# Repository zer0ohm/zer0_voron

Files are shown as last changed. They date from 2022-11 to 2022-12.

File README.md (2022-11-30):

# zer0_voron
## About zer0_voron
A repository for compiling modified parts, or a [hashtag](https://twitter.com/search?q=%23zer0_voron) to be added to tweets about VORON.

## BOM
Under development: It is a modification of an existing component, but it has never been tested and is "very" experimental. (To be tested soon, but undecided.)
### Shoiko(背負子)
 * Rear mounting of electrical components mod for VORON2.4
 * din_rail_mount_a/b inspired from [SnakeOil-XY](https://github.com/SnakeOilXY/SnakeOil-XY/blob/master/BETA2_Release/STLs/Panels/Back-panel/Bottom/4x_din-holder.stl)
 
| Part | Qty | Sourcing | Description/Note |
|---|---|---| --- |
| din_rail_mount_x2 | 2 | Print part([STEP](./CAD/din_rail_mount_x2.step) or [STL](./STLs/din_rail_mount_x2.stl)) |  |
| SHCS M3x** | 2 | Local store | Length are TBD. |
| M3 Roll-in T-Nut | 2 | [AliExpress](https://www.aliexpress.com/item/32805163712.html) |  |
| SB2040 Cable-harness <br> or <br> 2-wire 18AWG Robot Cable(3 meter) + 2-wire AWG22 Robot Cable(3 meter) | 1 | [AliExpress](https://www.aliexpress.com/item/1005004819126687.html) <br> or <br> [Misumi(AWG18)](https://jp.misumi-ec.com/vona2/detail/222000262826/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) + <br> [Misumi(AWG22)](https://jp.misumi-ec.com/vona2/detail/222000262826/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)| Length are TBD. See [Cable Processing](./Docs/cable_processing.md) |
| RJ11 Cable | 1 | [Misumi](https://jp.misumi-ec.com/vona2/detail/110500076440/?HissuCode=CBLRJ050-666-S-07-SV) | For BTT Octopus only. See [Cable Processing](./Docs/cable_processing.md) |
| Toolhead PCB | 1 | [AliExpress](https://www.aliexpress.com/item/1005004675264551.html) | AliExpress's link is example for in Stealthburner. |
| BHCS M5x10 | 2 | Stock or Local store | Replace of screws due to removal of "XY Cable Chain Bridge". |

### Modified Corner Brackets
 * Attempt to determine if printed brackets can be used to strengthen rigidity
 * model based Misumi's HBLFSN5(2mm narrower to avoid interference with Z_Idler)

| Part | Qty | Sourcing | Description/Note |
|---|---|---| --- |
| 2020Frame Corner Bracket 18mmWide | 12 | Print part([STEP](./CAD/2020_CornerBracket_18mm_x12.step) or [STL](./STLs/2020_CornerBracket_18mm_x12.stl)) ||
| SHCS M5x10 | 24 | Local store |  |
| M5 Roll-in T-Nut | 24 | [AliExpress](https://www.aliexpress.com/item/32805163712.html) |  |
| z_belt_cover_a_x2 | 2 | Print part([STEP](./CAD/z_belt_cover_a_x2_mod.step) or [STL](./STLs/z_belt_cover_a_x2_mod.stl)) | Use existing screws and nuts for mounting. |
| z_belt_cover_b_x2 | 2 | Print part([STEP](./CAD/z_belt_cover_b_x2_mod.step) or [STL](./STLs/z_belt_cover_b_x2_mod.stl)) | Use existing screws and nuts for mounting. |

### XYEndstop PCB for X_Carriage
 * Endstop PCB utilizing the switch mounting holes on the back side of X_Carriage 

| Part | Qty | Sourcing | Description/Note |
|---|---|---| --- |
| Endstop PCB | 1 | order PCB yourself([KiCad](./KiCad/V2-X_carriage_XYEndSW)) or [Single item PCB from me](https://zer0ohm.booth.pm/) ||
| Self-tapping screw M2x12 or M2x14 | 2 | Local store or [AliExpress](https://www.aliexpress.com/item/1005002306042593.html) | PCB mount screw |
| D2F-L3-A1 microswitch | 1 | Digikey or Mouser or Local store | X Endstop |
| D2F-L3 microswitch | 1 | Digikey or Mouser or Local store | Y Endstop |
| JST-XH S3B-XH-A | 1 | Digikey or Mouser or Local store |  |
| JST XH XHP-3 | 1 | Digikey or Mouser or Local store | Qty is the number used on this PCB only, the number may vary depending on the connection point. |

### Front Skirt PowerUI Mod(for 350mm build only)
 * Mod to bring "inlet and switch"(PowerUI) to front skirt
 * Can divert parts used in existing front_skirt_a and power_inlet_filtered

| Part | Qty | Sourcing | Description/Note |
|---|---|---| --- |
| front_skirt_a_mod | 1 | Print part([STEP](./CAD/front_skirt_a_mod.step) or [STL](./STLs/front_skirt_a_mod.stl)) ||
| [Optional] power_inlet_filtered_mod | 1 | Print part([STEP](./CAD/power_inlet_filtered_mod.step) or [STL](./STLs/power_inlet_filtered_mod.stl)) | Optional part. May use original parts. |

## Klipper_Configs
* Config for BTT Octopus+Mellow SB2040
* based [VORON's config](https://github.com/VoronDesign/Voron-2/blob/Voron2.4/firmware/klipper_configurations/Octopus/Voron2_Octopus_Config.cfg) and [Mellow/KlipperCN's config](https://mellow.klipper.cn/#/board/fly_sb2040/cfg)

| File | Description/Note |
|---|---|
| printer.cfg | |
| steppers.cfg | XYZ motor drive settings |
| toolhead.cfg | SB2040 settings |
| octopus_heatmanage.cfg | Bed-heater and FAN(excl toolhead fans) control |
| neopixel.cfg | lighting settings in chamber |
| macros.cfg | |
| display.cfg | BTT Mini12864 settings |

## What is Shoiko?
Shoiko(背負子)  is an Japanese word meaning "backpack". (naming inspired from [Kirigami](https://github.com/christophmuellerorg/voron_0_kirigami_bed).)

## License
This design are partially derived from the existing Voron parts and hence follow the same License, [GNU GPLv3](https://www.gnu.org/licenses/gpl-3.0.html).

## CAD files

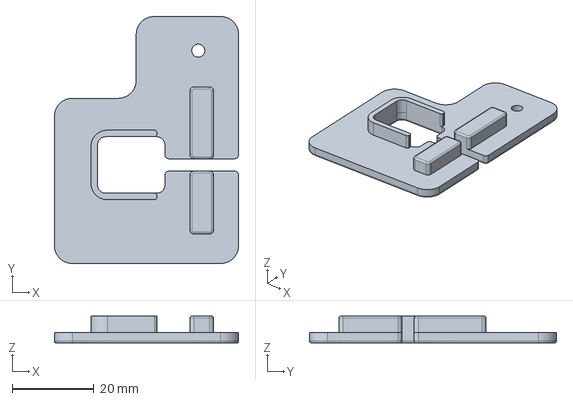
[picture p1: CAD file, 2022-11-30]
CAD/z_belt_cover_a_x2_mod.step
45.0 x 60.4 x 6.60 mm

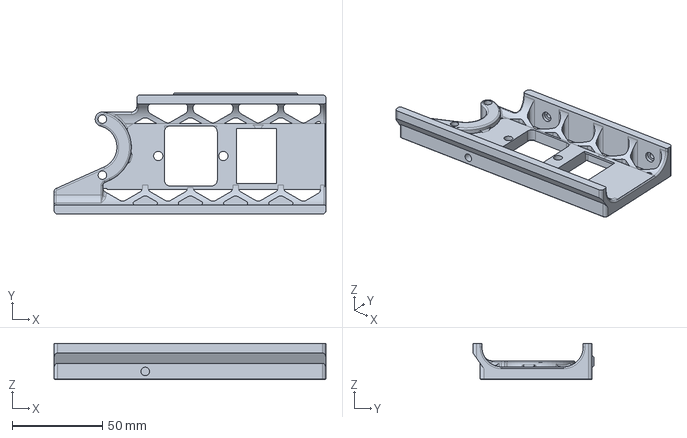
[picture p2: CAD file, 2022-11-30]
CAD/front_skirt_a_mod.step
150.5 x 67.0 x 20.0 mm

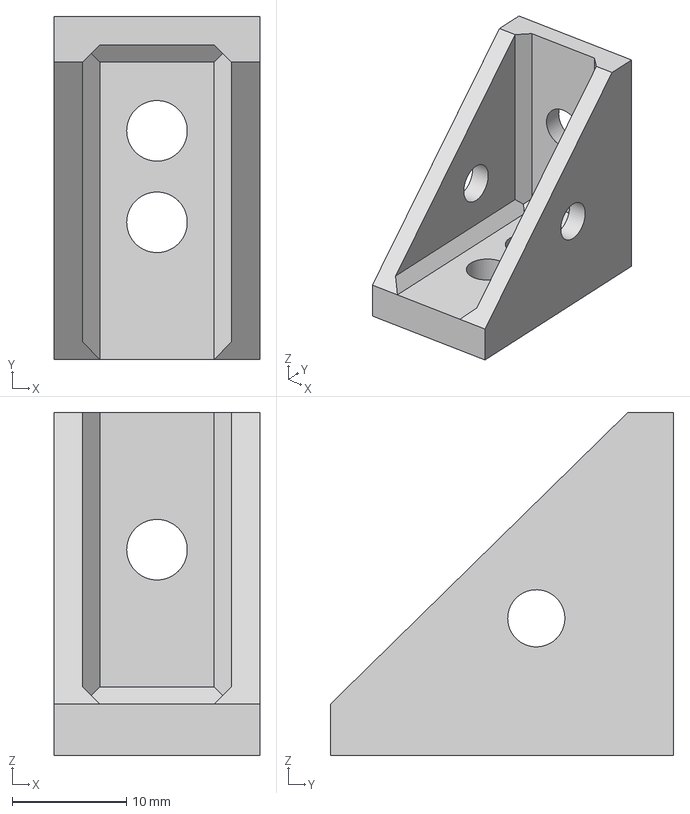
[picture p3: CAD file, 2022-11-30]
CAD/2020_CornerBracket_18mm_x12.step
18.0 x 30.0 x 30.0 mm

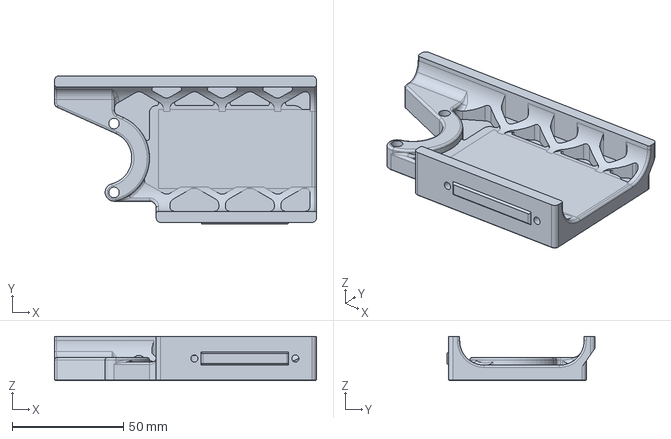
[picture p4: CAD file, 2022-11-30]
CAD/power_inlet_filtered_mod.step
118.0 x 66.8 x 20.0 mm

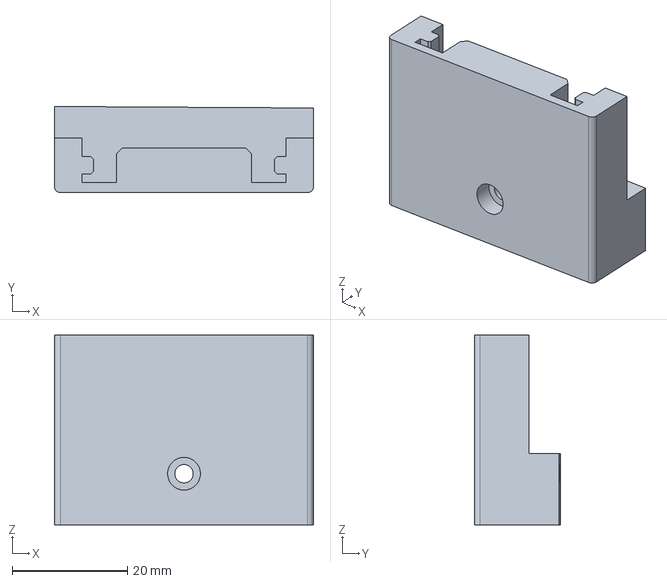
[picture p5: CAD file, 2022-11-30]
CAD/din_rail_mount_x2.step
45.0 x 15.0 x 33.0 mm

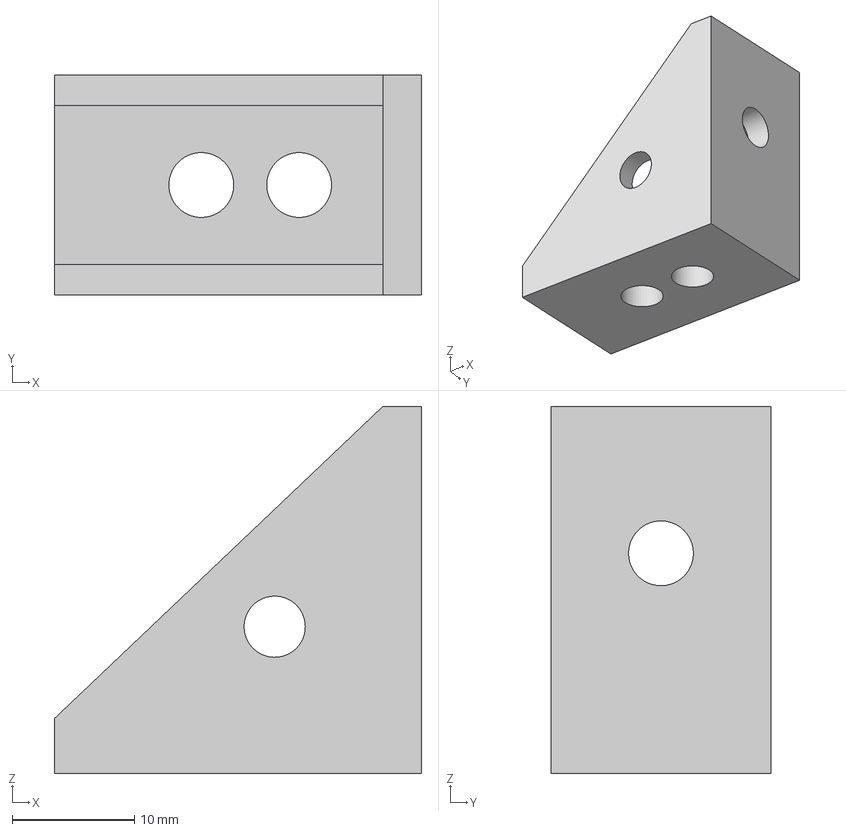
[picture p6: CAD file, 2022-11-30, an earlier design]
CAD/__archive/2020_CornerCube-18mm.step
30.0 x 18.0 x 30.0 mm

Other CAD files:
CAD/z_belt_cover_b_x2_mod.step
CAD/__archive/2020_CornerCube-18mm.f3d
STLs/2020_CornerBracket_18mm_x12.stl
STLs/din_rail_mount_x2.stl
STLs/front_skirt_a_mod.stl
STLs/z_belt_cover_b_x2_mod.stl

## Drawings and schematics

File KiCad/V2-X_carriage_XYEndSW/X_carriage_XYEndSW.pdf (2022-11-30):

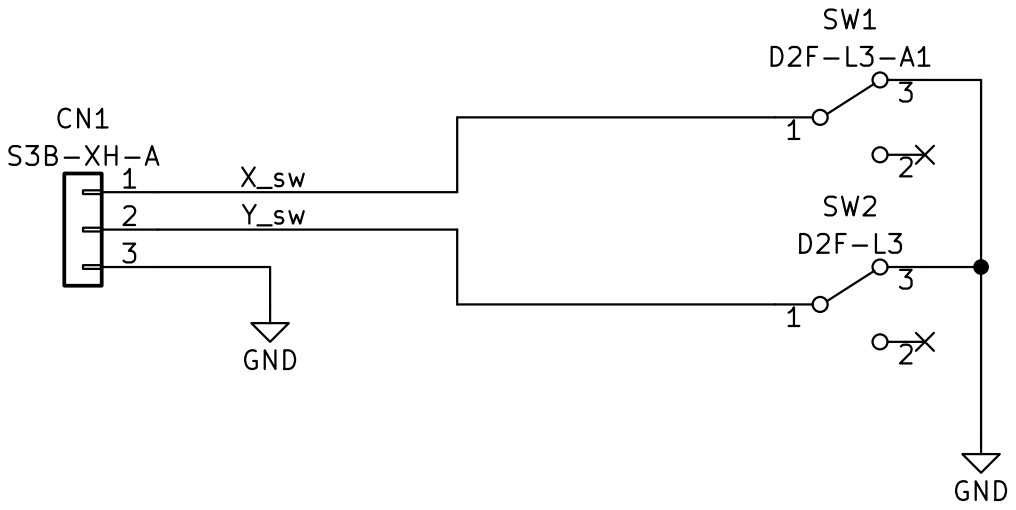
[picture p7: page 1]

File: X_carriage_XYEndSW.kicad_sch Sheet: / GND GND

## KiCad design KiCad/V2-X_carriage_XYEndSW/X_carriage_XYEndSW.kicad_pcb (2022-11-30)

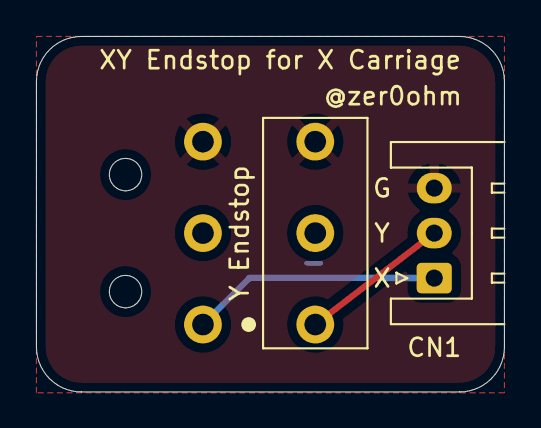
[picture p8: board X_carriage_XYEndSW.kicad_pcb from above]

Board: 2 copper layers, 26.0 x 19.8 mm, 3 parts (1 on the bottom side), 3 nets.

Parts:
CN1: S3B-XH-A; JST_XH_S3B-XH-A_1x03_P2.50mm_Horizontal
SW1: D2F-L3-A1; D2F-x_A1
SW2: D2F-L3; D2F-x_T

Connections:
/X_sw: CN1.1, SW1.1 (A)
/Y_sw: CN1.2, SW2.1 (B)
GND: CN1.3, SW1.3 (B), SW2.3 (A)

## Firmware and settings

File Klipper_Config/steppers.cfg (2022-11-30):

#####################################################################
#   X/Y Stepper Settings (G-Zeroのモータ制御設定を持ってくる予定)
#####################################################################

##  B Stepper - Left
##  Connected to MOTOR_0
##  Endstop connected to DIAG_0
[stepper_x]
step_pin: PF13
dir_pin: !PF12
enable_pin: !PF14
rotation_distance: 40
microsteps: 32
full_steps_per_rotation:200  #set to 400 for 0.9 degree stepper
endstop_pin: PG6
position_min: 0
##--------------------------------------------------------------------

##  Uncomment for 350mm build
position_endstop: 350
position_max: 350

homing_speed: 25   #Max 100
homing_retract_dist: 5
homing_positive_dir: true

##  Make sure to update below for your relevant driver (2208 or 2209)
[tmc2209 stepper_x]
uart_pin: PC4
interpolate: true # default: false
run_current: 0.8 # 1.2(If you use LDO-42STH48-2504AC)
sense_resistor: 0.110
stealthchop_threshold: 0

##  A Stepper - Right
##  Connected to MOTOR_1
##  Endstop connected to DIAG_1
[stepper_y]
step_pin: PG0
dir_pin: !PG1
enable_pin: !PF15
rotation_distance: 40
microsteps: 32
full_steps_per_rotation:200  #set to 400 for 0.9 degree stepper
endstop_pin: PG9
position_min: 0
##--------------------------------------------------------------------

##  Uncomment for 350mm build
position_endstop: 350
position_max: 350

homing_speed: 25  #Max 100
homing_retract_dist: 5
homing_positive_dir: true

##  Make sure to update below for your relevant driver (2208 or 2209)
[tmc2209 stepper_y]
uart_pin: PD11
interpolate: true # default: false
run_current: 0.8
sense_resistor: 0.110
stealthchop_threshold: 0
 
#####################################################################
#   Z Stepper Settings
#####################################################################

## Z0 Stepper - Front Left
##  Connected to MOTOR_2
##  Endstop connected to DIAG_2
[stepper_z]
step_pin: PF11
dir_pin: !PG3
enable_pin: !PG5
rotation_distance: 40
gear_ratio: 80:16
microsteps: 32
endstop_pin: PG10
##  Z-position of nozzle (in mm) to z-endstop trigger point relative to print surface (Z0)
##  (+) value = endstop above Z0, (-) value = endstop below
##  Increasing position_endstop brings nozzle closer to the bed
##  After you run Z_ENDSTOP_CALIBRATE, position_endstop will be stored at the very end of your config
position_endstop: -0.5
##--------------------------------------------------------------------

##  Uncomment below for 350mm build
position_max: 310

##--------------------------------------------------------------------
position_min: -5
homing_speed: 8
second_homing_speed: 3
homing_retract_dist: 3

##  Make sure to update below for your relevant driver (2208 or 2209)
[tmc2209 stepper_z]
uart_pin: PC6
interpolate: true # default: false
run_current: 0.8
sense_resistor: 0.110
stealthchop_threshold: 0

##  Z1 Stepper - Rear Left
##  Connected to MOTOR_3
[stepper_z1]
step_pin: PG4
dir_pin: PC1
enable_pin: !PA0
rotation_distance: 40
gear_ratio: 80:16
microsteps: 32

##  Make sure to update below for your relevant driver (2208 or 2209)
[tmc2209 stepper_z1]
uart_pin: PC7
interpolate: true # default: false
run_current: 0.8
sense_resistor: 0.110
stealthchop_threshold: 0

##  Z2 Stepper - Rear Right
##  Connected to MOTOR_4
[stepper_z2]
step_pin: PF9
dir_pin: !PF10
enable_pin: !PG2
rotation_distance: 40
gear_ratio: 80:16
microsteps: 32

##  Make sure to update below for your relevant driver (2208 or 2209)
[tmc2209 stepper_z2]
uart_pin: PF2
interpolate: true # default: false
run_current: 0.8
sense_resistor: 0.110
stealthchop_threshold: 0

##  Z3 Stepper - Front Right
##  Connected to MOTOR_5
[stepper_z3]
step_pin: PC13
dir_pin: PF0
enable_pin: !PF1
rotation_distance: 40
gear_ratio: 80:16
microsteps: 32

##  Make sure to update below for your relevant driver (2208 or 2209)
[tmc2209 stepper_z3]
uart_pin: PE4
interpolate: true # default: false
run_current: 0.8
sense_resistor: 0.110
stealthchop_threshold: 0

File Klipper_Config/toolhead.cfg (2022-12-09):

## SB2040 Board Initialization
[mcu sb2040]
canbus_uuid:  *3251a329e6e3*

#####################################################################
# Temperature Sensing
#####################################################################
## SB2040 MCU Temperatures => RP2040チップ内にある温度センサ
[temperature_sensor FLY_RP2040]
sensor_type: temperature_mcu
sensor_mcu: sb2040

## On-board NTC100K Thermistor => 雰囲気温度用
[temperature_sensor Chamber_Ambient]
sensor_type = ATC Semitec 104GT-2
sensor_pin = sb2040:gpio26
min_temp: -50
max_temp: 350

#####################################################################
# FAN controlls
#####################################################################
## FAN0 => Part Fan(5015 blower)
[fan]
pin: sb2040:gpio13
kick_start_time: 0.5
##  Depending on your fan, you may need to increase this value
##  if your fan will not start. Can change cycle_time (increase)
##  if your fan is not able to slow down effectively
off_below: 0.10

## FAN1 => Hotend Fan(4010 fan)
[fan_generic fan]
pin: sb2040:gpio14
max_power: 1.0
kick_start_time: 0.5
heater: extruder
heater_temp: 50.0
##  If you are experiencing back flow, you can reduce fan_speed
#fan_speed: 1.0

## FAN2 => None(reserved)
# [fan_generic fan]
# pin: sb2040:gpio15

#####################################################################
# XY endstop
#####################################################################
## SB2040では3本のGPIO(GPIO25, GPIO28, GPIO29)が使用でき, そのうちGPIO25は"高電圧"入力が可能である. そのため配線状況に応じてどのGPIOを使用するか選ぶこと. 
[stepper_x]
endstop_pin: ~sb2040:gpio29

[stepper_y]
endstop_pin: ~sb2040:gpio28

#####################################################################
# Probe
#####################################################################
[probe]
##  Inductive Probe
##  This probe is not used for Z height, only Quad Gantry Leveling

## Select the probe port by type:
## For the PROBE port. Will not work with Diode. May need pull-up resistor from signal to 24V.
#pin: ~!PB7
## For the DIAG_7 port. NEEDS BAT85 DIODE! Change to !PG15 if probe is NO.
#pin: PG15
## For Octopus Pro PROBE port; NPN and PNP proximity switch types can be set by jumper
#pin: ~!PC5

pin: sb2040:gpio25

#--------------------------------------------------------------------

x_offset: 0
y_offset: 25.0
z_offset: 0
speed: 10.0
samples: 3
samples_result: median
sample_retract_dist: 3.0
samples_tolerance: 0.006
samples_tolerance_retries: 3

#####################################################################
# Extruder (Driver: On-board TMC2209)
#####################################################################
[extruder]
step_pin: sb2040:gpio9
dir_pin: sb2040:gpio10
enable_pin: !sb2040:gpio7

##  Update value below when you perform extruder calibration
##  If you ask for 100mm of filament, but in reality it is 98mm:
##  rotation_distance = <previous_rotation_distance> * <actual_extrude_distance> / 100
##  22.6789511 is a good starting point

rotation_distance: 22.6789511   #Bondtech 5mm Drive Gears
##  Update Gear Ratio depending on your Extruder Type
##  Use 50:17 for Afterburner/Clockwork (BMG Gear Ratio)
##  Use 80:20 for M4, M3.1
gear_ratio: 50:17               #BMG Gear Ratio
microsteps: 32
full_steps_per_rotation: 200    #200 for 1.8 degree, 400 for 0.9 degree
nozzle_diameter: 0.400
filament_diameter: 1.75

[tmc2209 extruder]
uart_pin: sb2040:gpio8
interpolate: false
run_current: 0.500 # default_val=0.600
#sense_resistor: 0.110
stealthchop_threshold: 0 # default_val=999999

#####################################################################
# Hotend
#####################################################################
heater_pin: sb2040:gpio6
sensor_pin: sb2040:gpio27

## SB2040のサーミスタ監視ピンの既定プルアップ抵抗は4700(4.7k)Ωである. PT1000サーミスタを使用する場合は基板内のジャンパをショートさせることで1000(1k)Ωに変更可能.
sensor_type: PT1000
pullup_resistor: 1000
min_temp: 10
max_temp: 350
max_power: 1.0
min_extrude_temp: 170
control = pid
pid_kp = 26.213
pid_ki = 1.304
pid_kd = 131.721

##  Try to keep pressure_advance below 1.0
pressure_advance: 0.05
##  Default is 0.040, leave stock
pressure_advance_smooth_time: 0.040

#####################################################################
## RGB(Neopixel)
#####################################################################
[neopixel toolhead_neopixel]
pin: sb2040:gpio12
chain_count: 12
color_order: GRBW
initial_RED: 0.0
initial_GREEN: 0.0
initial_BLUE: 0.0

#####################################################################
# On-board ADXL345 Accelerometer
#####################################################################
[adxl345]
cs_pin: sb2040:gpio1
spi_software_sclk_pin: sb2040:gpio0
spi_software_mosi_pin: sb2040:gpio3
spi_software_miso_pin: sb2040:gpio2

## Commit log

2022-09-29 Add alpha version BOM
2022-10-02 Update README.md
    fix BOM
2022-11-30 add design/config files
    [2020_CornerBracket_18mm_x12.step, 2020_CornerBracket_18mm_x12.stl, 2020_CornerCube-18mm.f3d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]
2022-11-30 fix z_belt_cover filenames
    [z_belt_cover_b_x2_mod.stl]
